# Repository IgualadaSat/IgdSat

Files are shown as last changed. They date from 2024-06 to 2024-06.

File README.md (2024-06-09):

# IgdSat
The official source-code of IgdSat CanSat for you to build and improve at home!
This repo includes software, CAD and instructions on how to build it.

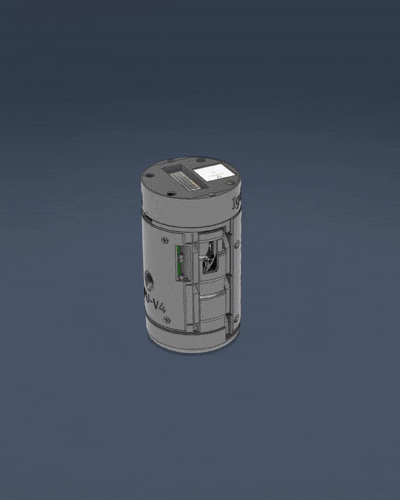
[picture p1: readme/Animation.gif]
gif1 Animation

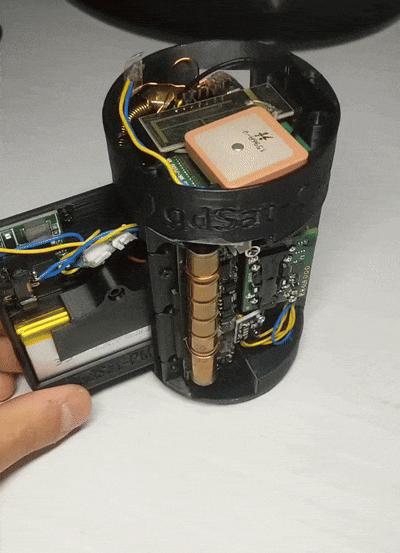
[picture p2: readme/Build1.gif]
gif2 Build1

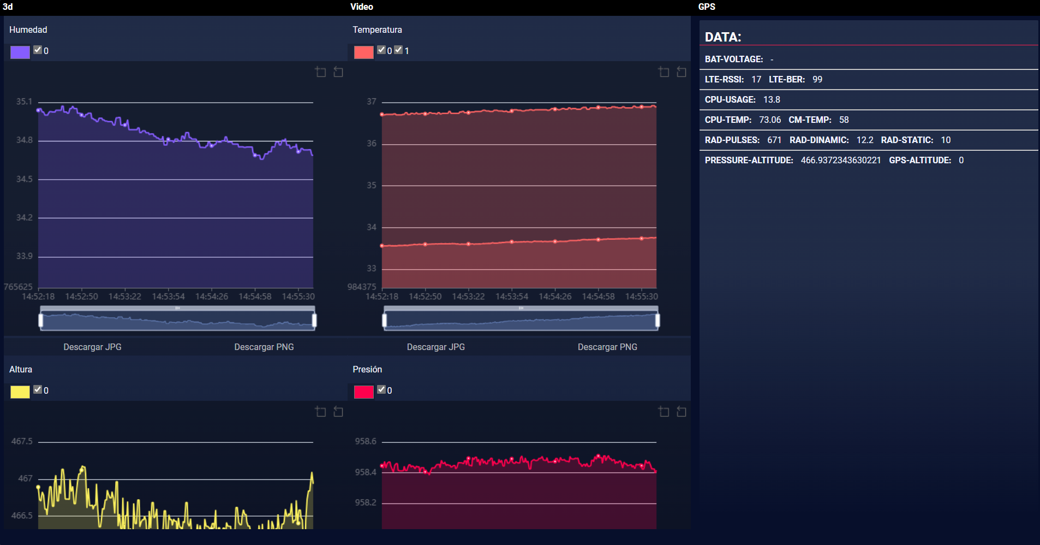
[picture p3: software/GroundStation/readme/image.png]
GS GS sample image


Follow us on social media!
 - Instagram: @cansat_igualada
 - TikTok: @igdsat
 - YouTube: @IgdSat

Join our discord server! https://discord.gg/XWwqkaNrvV

The repo structure is the following:

```
└── IgdSat/
    ├── Hardware (CAD)/
    │   ├── IgdSat-v2 --> Specific combination of modules
    │   └── Modules/ --> List of all modules
    │       ├── MPU
    │       ├── CM
    │       ├── PM
    │       ├── SM
    │       └── ...
    └── Software/
        ├── IgdSat --> Main code for IgdSat
        └── GroundStation --> Software of the web app
```

## Hardware:
The required hardware depends on which modules you want to build.
You can choose what features you want your IgdSat to have.
### Minimum hardware
- **Raspberry Pi Zero 2W** (22$) [Amazon](https://www.amazon.com/Raspberry-Quad-core-Bluetooth-onboard-Antenna/dp/B0CCRP85TR/)
- **Micro SD card** (8$) [Amazon](https://www.amazon.com/SanDisk-128GB-microSDXC-Memory-Adapter/dp/B08GY9NYRM/)
- **Battery switch** (0.1$/piece) [Amazon ES](https://www.amazon.es/dp/B086QGZRKG) [Amazon](https://www.amazon.com/Tnuocke-Vertical-Position-Latching-SS12F15-G5/dp/B099N3HFPG/)
- **Battery** (23€) [Amazon ES](https://www.amazon.es/dp/B09YQ393N2)
- **Battery charger/booster** (1.1$/piece) [Amazon](https://www.amazon.com/Adjustable-Lithium-Battery-Charger-Discharge/dp/B09WD9GCZC/)
- **M1-M2 self-threading screws** [Amazon](https://www.amazon.com/dp/B0CQJZH135/)
(and the PLA/PETG and TPU filament for 3D printing)

### Recomended hardware
- **4G GSM Module** (26.26$ or 31.28€) [Aliexpress](https://aliexpress.com/item/4000449295553.html)
- **APC220 RF Pair** (26.56$ or 31.01€) [Aliexpress](https://aliexpress.com/item/1005001710399951.html)
- **BMP280 sensor** (1.48$/piece or 1.7€/piece) [Amazon](https://www.amazon.com/HiLetgo-Precision-BMP280-3-3-Atmospheric-Pressure/dp/B07VNDZ6N4/) [Amazon ES](https://www.amazon.es/dp/B0BN1NXG4D)
- **Raspberry Pi Camera Module v3 Wide** (25.99$ or 39.95€) [Amazon](https://www.amazon.com/Arducam-Raspberry-Camera-Module-IMX708/dp/B0D2QK3QXQ/) [ES Tiendatec](https://www.tiendatec.es/raspberry-pi/camaras/1986-camara-oficial-raspberry-pi-v3-12mpx-wide--5056561800363.html) (You also have to buy the [CSI adapter](https://www.tiendatec.es/raspberry-pi/cables/1750-cable-flex-csi-camara-raspberry-pi-zero-38mm-8472496021678.html) as it's sold separately) 
- **Active Buzzer** (0.4$/piece) [Amazon](https://www.amazon.com/HiLetgo-Integrated-Sounder-Speaker-Electromagnetic/dp/B09L4M84M9/)
- **LED** Standard size
  
### Optional hardware
- **Sensirion SCD30 CO2 sensor** (14.84$ or 17.33€) [Aliexpress](https://aliexpress.com/item/1005004541153141.html)
- **RadSens radiation sensor** (53$) [Tindie](https://www.tindie.com/products/climateguard/dosimeter-with-i2c-radsens-arduino/)

## Software:
The source-code for the software is provided "AS IS" and it's documentation is under development. Despite that, it's all tested to work properly.
The main code for IgdSat's Raspberry Pi is tested to work on a clean `Raspberry Pi OS Lite` installation after the execution of the install.sh bash script with sudo privileges.
The instructions on how to use the Ground Station is listed on it's README.md file.

# Disclaimer
All the software on this repository is under the GNU GENERAL PUBLIC LICENSE. You're free to use, modify and share but you can't take possession of it; every distribution of this software should maintain the same license and mention it's author.
We appreciate every type of contribution to this project. You can submit issues, pull requests and create forks. For any questions about this project, check the FAQ and/or enter our discord server.

# FAQ
## What is IgualadaSat?
IgualadaSat is a project driven by 7 High School students with the aim of building a device to **compete in the CanSat competition**.  :rocket: 
We are a team from Catalonia, Spain with a passion for **tech** and **aerospace** :milky_way: so we decided to share our achievements with the international community :globe_with_meridians:

## What is CanSat?
*Extracted from cansat.esa.int *
A CanSat is a simulation of a real satellite, integrated within the volume and shape of a soft drinks can. The challenge for the students is to fit all the major subsystems found in a satellite, such as power, sensors, and a communication system, into this minimal volume. The CanSat is then launched by a rocket up to an altitude of approximately one kilometer, or dropped from a platform, drone, or captive balloon. During its descent, it should carry out a scientific experiment and/or a technology demonstration, achieving a safe landing, and analyzing the data collected.

## How is it structured?
It is structured with a **modular design**, so it speeds up the prototyping process and makes it easier to 3D print.  They are all fixed to the Main-Frame Module with self-threading screws. IgdSat consists of 6 modules:
- **Communication Module V4** (CM):  Integrates the necessary transceivers, receivers and antennas. *(SIM7600G-H, APC220 and antennas)*
- **Main Processing Unit V4** (MPU): Integrates the main computer and the HD camera, as well as a buzzer and an LED for debugging and recovery. *(Raspberry Pi Zero 2W, Raspberry Pi Camera Module v3 Wide)* 
- **Sensorial Module V2** (SM): Integrates the I2C sensors, such as radiation, temperature, humidity, pressure, and CO2 sensors. *(RadSens, SCD-30 and BMP280)*
- **Power Module V2** (PM): Integrates all the power-related components. This version uses a Li-ion battery* ( 3,7V 3000mAh li-ion battery, a switch and a charger and 5V booster)
- **Main Frame V2** (MF): Just a rigid plastic piece. It mechanically connects all the modules and ensures the proper integrity of the CanSat.
- **Amortiguation Module V1** (AM): Another integrity module to absorb the impact of landing. It is meant to be 3D printed with TPU or other similar flexible materials and with a special infill and specific printer settings.

\* We are working on a different Power Module that uses AA batteries

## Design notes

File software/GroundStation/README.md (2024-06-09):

# Cansat 2024 Groundstation

The official IgdSat-GS (IgualadaSat Ground Station)
A web app based on Javascript Vanilla using node-modules such as echarts and express
Developed by @trmaa

The application is still in development.

sample image

## Installation

Make sure you have npm and node (v21.7) installed. 
You can install it through the webpage: https://nodejs.org/en/download/package-manager

Then install the dependencies with ´npm install´

To properly connect to IgdSat, you will have to replace the IP with the one you use for IgdSat in your environment in the following files: dist\public\components\video.html and dist\public\src\ws.js

Finally, just execute `node server` to start the web server!

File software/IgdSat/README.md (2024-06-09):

# IgdSat software

The official IgdSat software.
It's the main code for the IgualadaSat Main-Processing-Unit ( based on Raspberry pi zero 2W) using Python3

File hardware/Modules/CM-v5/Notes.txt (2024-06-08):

The CM-v5-cover must be 3d printed with -0.15mm or -0.2mm horitzontal expansion in order to fit in the main module.
There's no tolerance added on the cover and therefore you should have to test what works best for you.

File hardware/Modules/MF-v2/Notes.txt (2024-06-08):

It's important to 3D print it with 100% infill.

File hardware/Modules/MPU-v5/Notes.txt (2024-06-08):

The MPU-v5-CameraSupportWide only works for the Raspberry Pi Camera Module v3 Wide, because the camera lens is bigger. 
For non-Wide models, use the standard version MPU-v5-CameraSupport.

You should 3d print the pieces with the predominant flat surface touching the buildplate. 
In the case of the MPU-v5-Cover it is already correctly oriented, for this piece you may want to reduce the printer speed and (maybe) add a brim due to the small flat surface.

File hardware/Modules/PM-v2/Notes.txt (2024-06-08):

You can use 100-20% infill but 100% is recommended.
The main PM-v2 is already oriented correctly for 3D printing

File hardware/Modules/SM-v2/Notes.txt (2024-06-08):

This is the most dispensable/modifiable module.
Newer versions of this module ( using other sensors ) will be developed later on.
The SM-v2-Cover is the only piece of IgdSat that needs supports to 3D print, you should flip it upside-down and add the most basic support with a little of brim also.

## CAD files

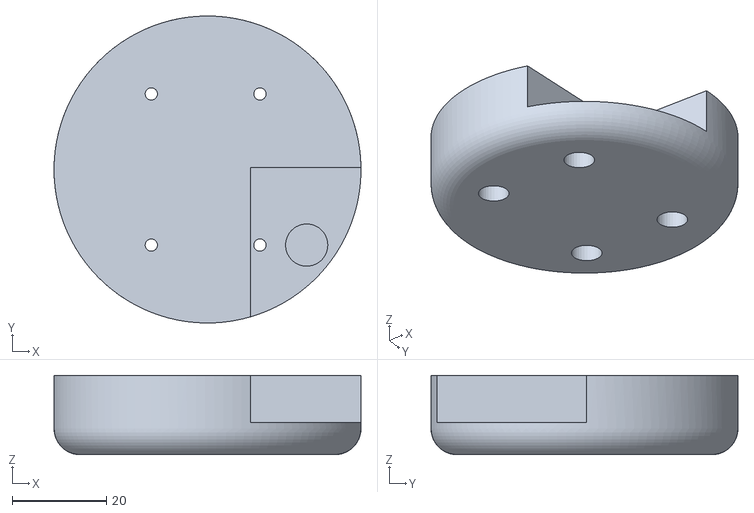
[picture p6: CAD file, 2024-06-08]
hardware/Modules/AM-v2/AM-v2.stl
65.0 x 65.0 x 16.8

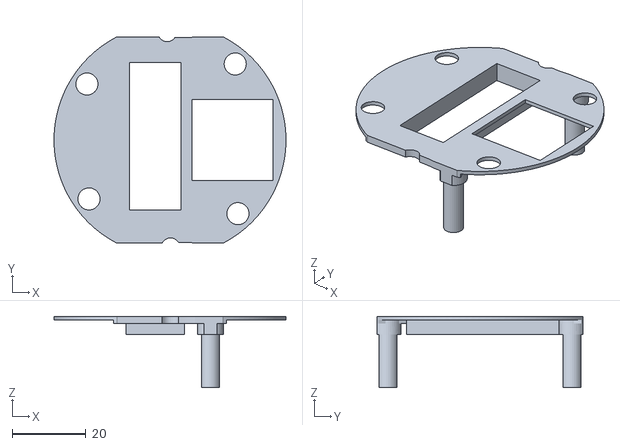
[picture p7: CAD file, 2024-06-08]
hardware/Modules/CM-v5/CM-v5-cover.stl
63.0 x 56.0 x 19.4

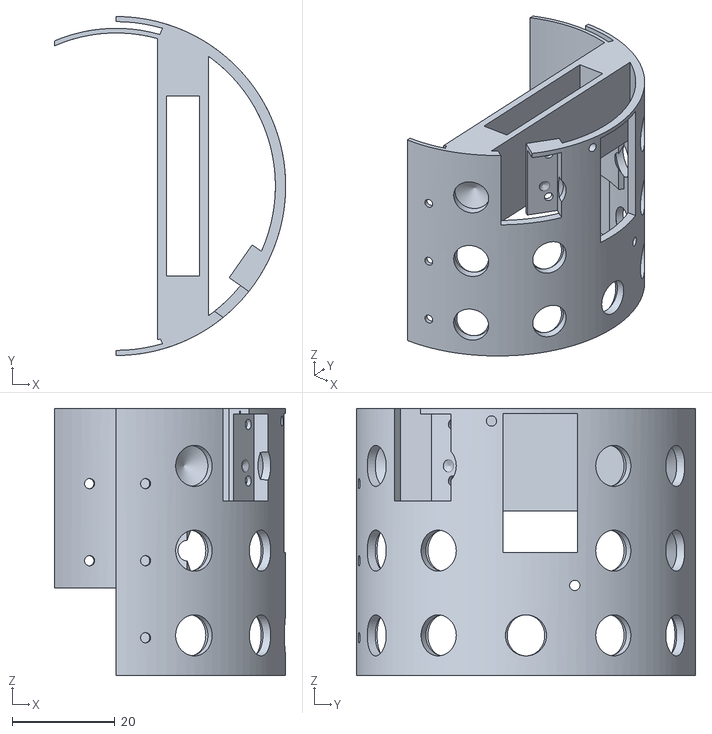
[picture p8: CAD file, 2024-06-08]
hardware/Modules/IM-v1/IM-v1-Cover.stl
45.0 x 66.0 x 52.0

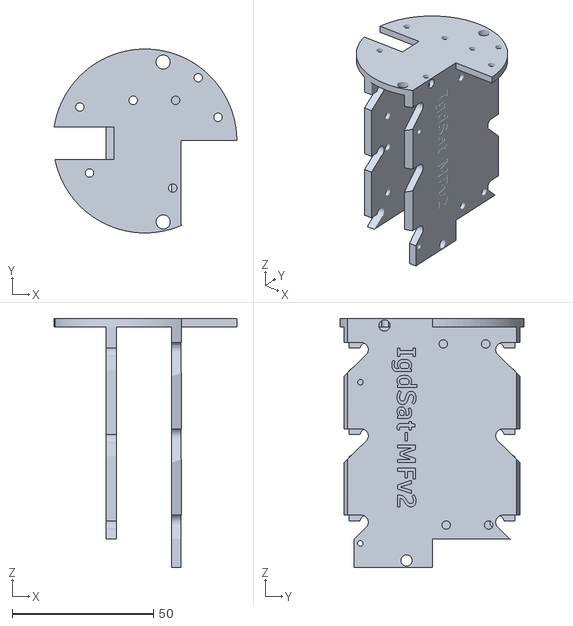
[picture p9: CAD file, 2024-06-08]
hardware/Modules/MF-v2/MF-v2.stl
64.6 x 65.0 x 88.0

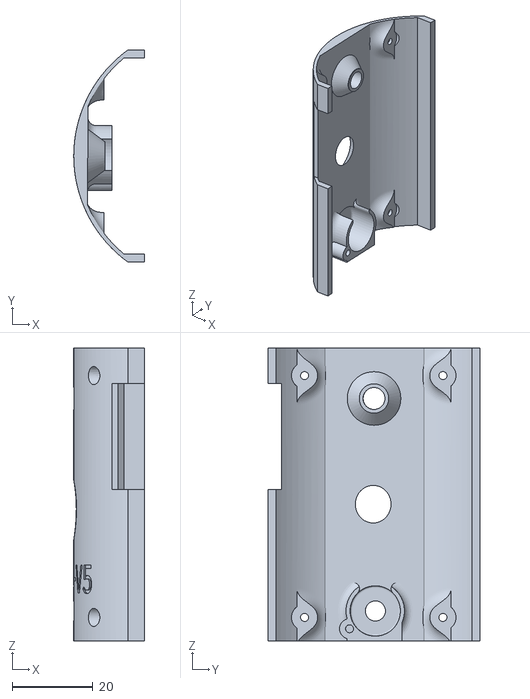
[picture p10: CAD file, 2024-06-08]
hardware/Modules/MPU-v5/MPU-v5-Cover.stl
17.5 x 52.7 x 72.7

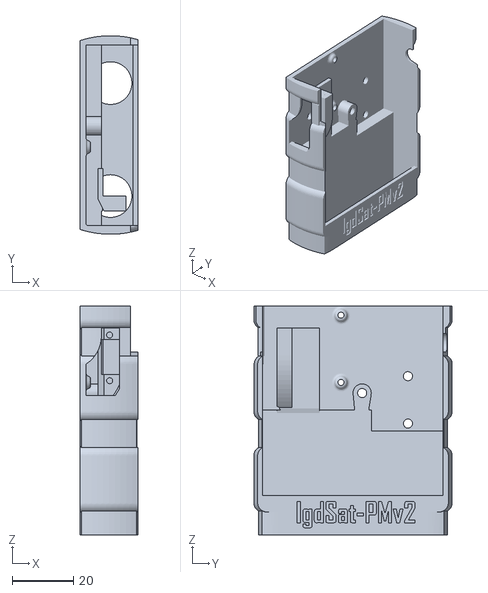
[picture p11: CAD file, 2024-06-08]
hardware/Modules/PM-v2/PM-v2.stl
19.0 x 65.0 x 75.0

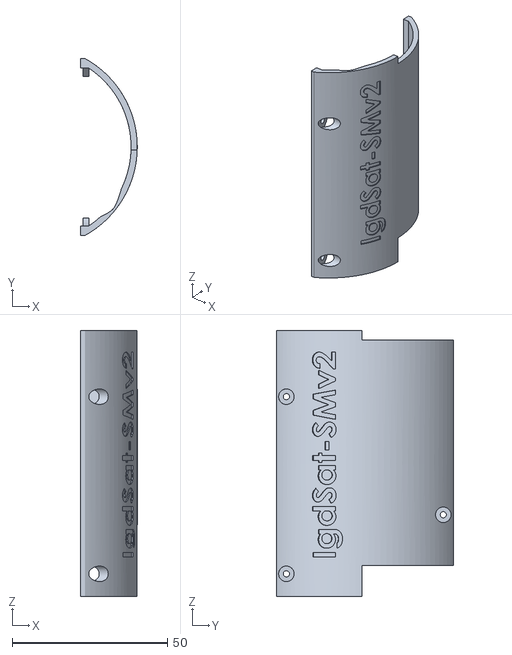
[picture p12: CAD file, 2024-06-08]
hardware/Modules/SM-v2/SM-v2-Cover.stl
18.2 x 57.0 x 85.6

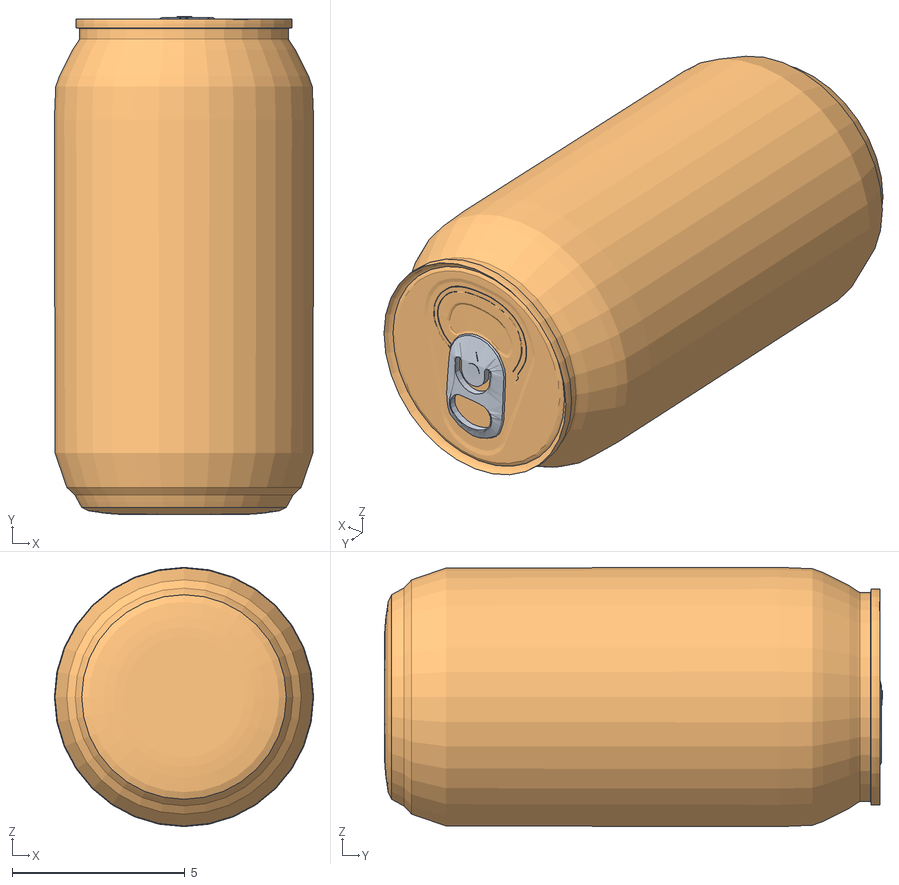
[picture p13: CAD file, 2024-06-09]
software/GroundStation/dist/public/storage/igdsat.obj
7.50 x 14.4 x 7.50
Plane.001_Plane.002

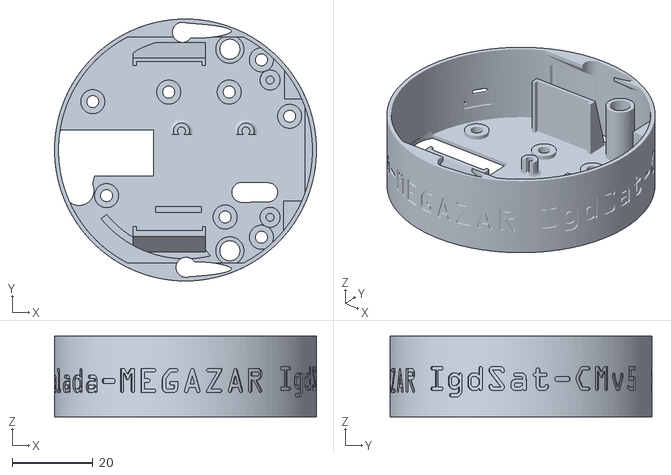
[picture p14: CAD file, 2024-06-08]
hardware/Modules/CM-v5/CM-v5.stl
65.0 x 65.0 x 20.0

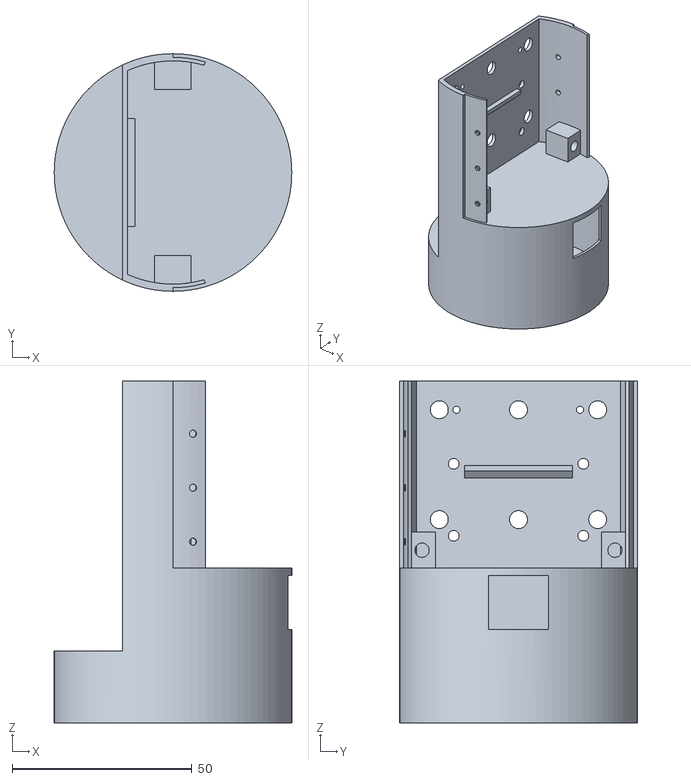
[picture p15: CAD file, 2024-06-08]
hardware/Modules/IM-v1/IM-v1.stl
66.0 x 66.0 x 95.0

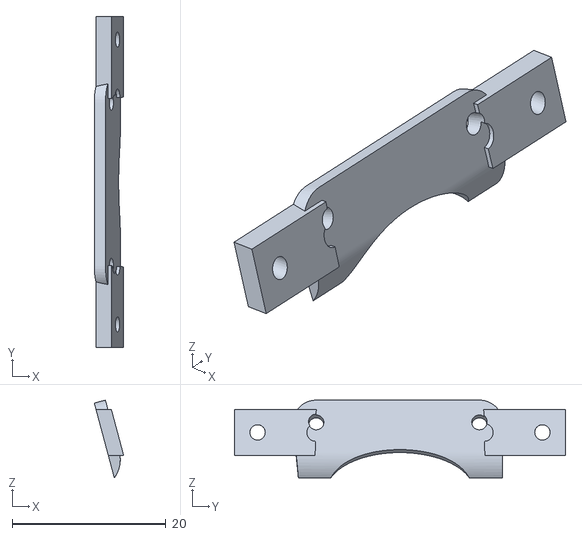
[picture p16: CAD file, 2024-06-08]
hardware/Modules/MPU-v5/MPU-v5-CameraSupportWide.stl
3.83 x 43.0 x 10.1

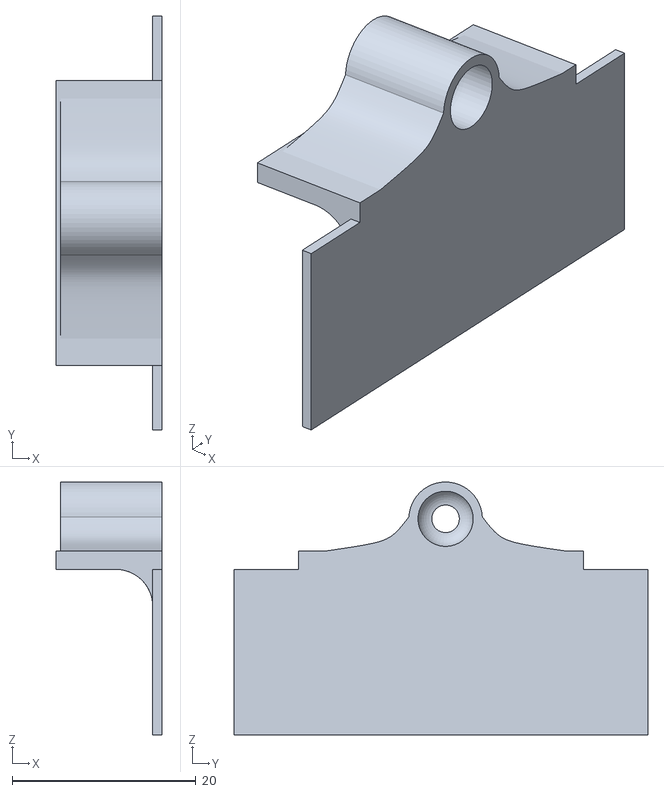
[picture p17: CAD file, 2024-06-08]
hardware/Modules/PM-v2/PM-v2-BatteryLid.stl
11.5 x 45.0 x 27.5

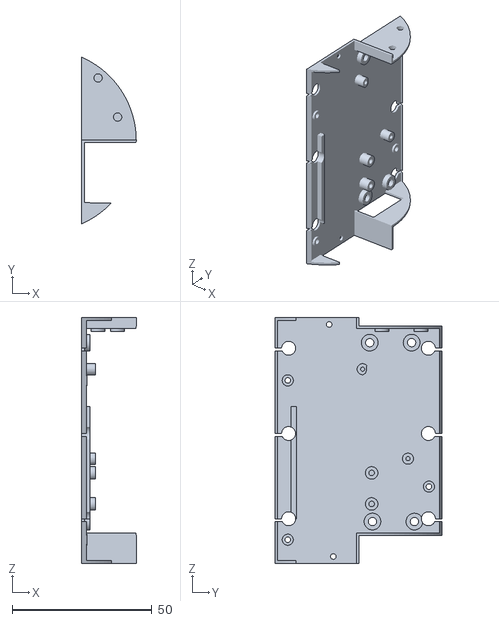
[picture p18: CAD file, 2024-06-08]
hardware/Modules/SM-v2/SM-v2.stl
19.5 x 59.6 x 88.0

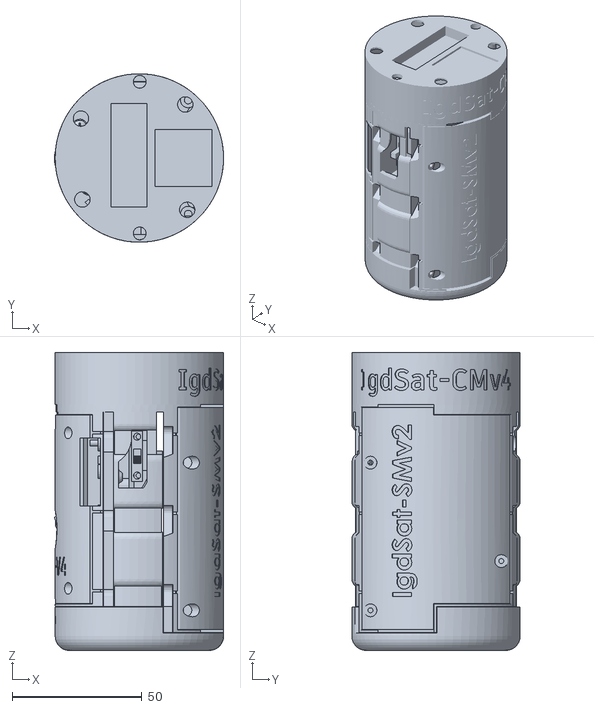
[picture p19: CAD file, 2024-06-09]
software/GroundStation/dist/public/storage/IgualadaSat-v2-preview.stl
65.3 x 65.0 x 115.0

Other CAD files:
hardware/Modules/MPU-v5/MPU-v5-CameraSupport.stl
software/GroundStation/dist/public/storage/fusion_cansat_Frame.obj
hardware/Modules/MPU-v5/MPU-v5.stl

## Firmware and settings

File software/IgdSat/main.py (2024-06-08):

#!/usr/bin/env python

import asyncio
import itertools
import json
import websockets
import subprocess

print("Initializing IgdSat...")
#IgdSat scripts...
from outputs import *

from sensors import *
from camera import *
from APC import APC

class IgdSat():
    def __init__(self) -> None:
        self.outputs = Outputs()
        self.bmp = None
        self.sensirion = None
        self.CM = CommunicationModule()
        self.RadSens = None
        #DATA = [0,0,0,0,0,0,0,0,0,0] # 0 - co2, 1- temp1, 2- humidity, 3- temp2, 4 - altitude, 
        #                        #  5 - rad_d, 6 - GpsLat, 7 - GpsLong, 8 - rad_s, 9 - rad_pulses
        #                        #
        DATA = { # The data packet structure
            "U": [0], # Unix time
            "C": [0], # Co2
            "T": [0,0,0,0], # Temperature [BME, SCD-30, MPU-temp, CM-temp]
            "H": [0], # Humidity
            "A":[0,0], # Altitude [Pressure-based, GPS-based]
            "P":[0], # Barometric pressure
            "R": [0,0,0], # Radiation [Dinamic-rad,Static-rad, Pulses]
            "G": [0,0], # GPS [LAT, LONG]
            "S": [0,0], # Signal for LTE [RSSI signal, bit error rate]
            "D": [0] # Debuging [CPU-usage]
        }
        self.DATA = DATA
        self.Active = False # Active mode means High-Speed data collection during parachute descent
        self.apc = None

igdsat = IgdSat()
encoder.igdsat = igdsat
igdsat.outputs.notes = [1100,2200,1100,2200]
igdsat.apc = APC(igdsat)
DATA=igdsat.DATA
# Websocket handler
async def handler(websocket):
    print("New connection")
    igdsat.outputs.notes = [1000,2000,3000,4000]
    igdsat.outputs.led = [1,0]
    try:
        while True:
            await websocket.send(json.dumps(DATA))
            Interval = 1
            if igdsat.Active:
                Interval = 0.5
            await asyncio.sleep(Interval)
    except Exception as e:
        igdsat.outputs.notes = [4000,3000,2000,1000]
        igdsat.outputs.led = [1,1,0,0]
        raise e

# Internet checker...
async def InternetCheck():
    failed=0
    while True:
        try:
            result = await asyncio.create_subprocess_shell("ping -c 2 -W 3 10.8.0.1", # To check that VPN works
                                                           stdout=subprocess.PIPE,
                                                           stderr=subprocess.PIPE)
            stdout, stderr = await result.communicate()

            if result.returncode == 0:
                failed = 0
                continue
            else:
                failed += 1
                if failed == 2:
                    failed = 0
                    # In case it fails --> restart VPN
                    igdsat.outputs.notes = [4400,0,4400,0,2200,0,2200,0,4400,0,4400,0,2200,0,2200,0]
                    await asyncio.create_subprocess_shell("sudo service openvpn restart", stdout=subprocess.PIPE, stderr=subprocess.PIPE)
                    await asyncio.sleep(3)

        except Exception as e:
            print("PING ERROR")
            continue

        await asyncio.sleep(2)

# Asyncio asyncronous execution
async def main():
    async with websockets.serve(handler, "", 8001):
        #await asyncio.Future()  # run forever
        await run_web_server()
        await asyncio.gather(  SensorsReading(igdsat), igdsat.CM.serve(), igdsat.outputs.serve(), InternetCheck() )


if __name__ == "__main__":
    asyncio.run(main())

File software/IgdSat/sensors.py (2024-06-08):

import asyncio
import time
import json
import os

#bmp280
import board
import busio
import adafruit_bmp280

#sensirion
from sensirion_i2c_driver import LinuxI2cTransceiver, I2cConnection, CrcCalculator
from sensirion_i2c_adapter.i2c_channel import I2cChannel
from sensirion_i2c_scd30.device import Scd30Device

# Raspberry pi internal features
import psutil # CPU usage 
import gpiozero as gz # CPU temperature 

# Other IgdSat scripts...
#   CommunicationModule
from CommunicationModule import *
#   RadSens
import RadSens

async def InitializeSensors(igdsat):

    #Activating bmp280...
    print("Activating bmp280...")
    try:
        i2c = busio.I2C(3, 2)
        igdsat.bmp = adafruit_bmp280.Adafruit_BMP280_I2C(i2c,118)
    except:
        print("ERROR: Couldn't connect to bmp280")
        print("Overriding temperature and pressure measurement...")
        igdsat.bmp = None

    #Activating sensirion...
    print("Activating sensirion...")
    i2c_transceiver = LinuxI2cTransceiver('/dev/i2c-1')
    tries=0
    while tries < 5:
        try:
            channel = I2cChannel(I2cConnection(i2c_transceiver),slave_address=0x61,crc=CrcCalculator(8, 0x31, 0xff, 0x0))
            
            igdsat.sensirion = Scd30Device(channel)
            sensirion = igdsat.sensirion
            sensirion.stop_periodic_measurement()
            sensirion.soft_reset()
            sensirion.start_periodic_measurement(0)
            break
        except:
            print("ERROR sensirion connection, retrying...")
            await asyncio.sleep(0.5)
            tries += 1
            continue
    if tries >= 5:
        print("ERROR: Couldn't connect to sensirion Scd30")
        print("Overriding C02 and humidity measurement...")
        igdsat.sensirion = None

    #Activating RadSens...
    igdsat.radSens = RadSens.CG_RadSens(RadSens.RS_DEFAULT_I2C_ADDRESS)
    radSens = igdsat.radSens
    radSens.init()
    tries=0
    while tries < 10 :
        if not radSens.init():
            tries += 1
            await asyncio.sleep(0.5)
            continue
        else:
            break
    if tries >= 10:
        print("ERROR: Couldn't connect to RadSens")
        print("Overriding radiation measurement...")
        igdsat.radSens = None
    else:
        radSens.set_sensitivity(105)
        await asyncio.sleep(0.5)
        radSens.set_hv_generator_state(False)
        await asyncio.sleep(0.5)
        radSens.set_led_state(True)


async def SensorsReading( igdsat):
    await InitializeSensors(igdsat)
    await igdsat.CM.initialize()
    data = igdsat.DATA

    ActiveIterator=0 # 2 Iterations at dv>1m/s # 20 iterations to make standby 
    
    PreviousAltitude=0
    Iterator=1 # 1 second for standby, 0.5 seconds for active
    with open(os.path.expanduser('~') + "/IgdSat-DATA/DATA.txt", "a") as DataFile:
        DataFile.write("\n\n\nNew session...")
        try:
            while True:

                await asyncio.sleep(Iterator)
                try:
                    sensirion = igdsat.sensirion
                    if sensirion:
                        (a,b,c) = sensirion.read_measurement_data()
                        if a==a: # Looks redundant but it's neccessary to check for nan values
                            #(co2_concentration, temperature, humidity) = a,b,c
                            data["C"][0] = a # co2
                            data["T"][1] = b # scd-30 temperature
                            data["H"][0] = c # humidity
                    bmp = igdsat.bmp
                    if bmp:
                    #(temp2, altitude) = (sensor.temperature,sensor.altitude)
                        data["T"][0] = bmp.temperature
                        data["A"][0] = bmp.altitude
                        data["P"][0] = bmp.pressure

                    #Raspberry Pi Internal
                    data["T"][2] = gz.CPUTemperature().temperature
                    data["D"][0] = psutil.cpu_percent()
                    data["U"][0] = time.time()

                    #CM
                    CM = igdsat.CM
                    if CM:
                        data["G"] = [CM.GPS[0],CM.GPS[1]] # GPS coordinates
                        data["A"][1] = CM.GPS[2] # GPS altitude
                        data["S"] = CM.Signal
                        data["T"][3] = CM.CPUTemp

                    #RadSens
                    radSens = igdsat.radSens
                    if radSens:
                        a = radSens.get_rad_intensy_dynamic()
                        b = radSens.get_rad_intensy_static()
                        c = radSens.get_number_of_pulses()
                        data["R"] = [a,b,c]

                    # Active calculation

                    if PreviousAltitude != 0:
                        altitude_difference = abs(data["A"][0] - PreviousAltitude)
                        if igdsat.Active == False:
                            if altitude_difference >= 1.0:
                                ActiveIterator += 1
                            else:
                                ActiveIterator = 0
                            if ActiveIterator >= 2:
                                igdsat.Active = True
                                Iterator = 0.5
                                ActiveIterator = 0
                                igdsat.outputs.notes = [4400,1100,4400,1100,4400,1100] # Activating
                        else:
                            if altitude_difference < 1.0:
                                ActiveIterator += 1
                            else:
                                ActiveIterator = 0
                            
                            if ActiveIterator >= 20: # Static for 20 iterations --> 10 seconds
                                igdsat.Active = False
                                Iterator = 1
                                ActiveIterator = 0
                                igdsat.outputs.notes = [1100,0,1100,0,1100,0,1100] # Deactivating

                    igdsat.apc.print(str([data["U"][0] ,data["C"][0], data["T"][0], data["A"][0], data["P"][0], data["R"][0], data["G"][0],data["G"][1] ]))

                    PreviousAltitude=data["A"][0]
                    DataFile.write(json.dumps(data) + "\n")


                except KeyboardInterrupt:
                    raise
                except:
                    print("ERROR: Sensor measurement error")
                    pass

                #text = ""
                #text += f"\nCo2: {data[0]}\nTemperature-1: {data[1]}\nHumidity: {data[2]}"
                #text += "\nTemperature-2: " + str(round(data[3], 2))
                #text += "\nAltitude: " + str(round(data[4], 2))
                #text += "\nRadSens: " + str(data[5])
                #print(text)
                

        except KeyboardInterrupt:
            print("\nKeyboardInterrupt!")
            print("Closing connections...")
            pass

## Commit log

2024-06-08 IgdSat software and hardware
    [AM-v2.stl, CM-v5-cover.stl, CM-v5.stl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]
2024-06-08 bug fixes before v1 1
    [CommunicationModule.py, main.py, outputs.py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]
2024-06-09 IgdSat bug fixes before launch 2
    [CommunicationModule.py]
2024-06-09 Added the GroundStation software!
    [IgualadaSat-v2-preview.stl, fusion_cansat_Frame.obj, igdsat.obj]
